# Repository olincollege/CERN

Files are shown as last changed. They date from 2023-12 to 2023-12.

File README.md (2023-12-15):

# CERN
ENGR 2110 Final Project: Centripetal Electronic Robotic Navigator (CERN)

#### Final Project by Ari Bobesh (Electrical), Venkadesh Eswaranandam (Electrical), Angela Huang (Mechancial), Sohum Kothavade (Mechanical), and Kevin Lie-Atjam (Firmware/Software)

Welcome to the Centripetal Electronic Robotic Navigator (CERN) project! In this repository, we embark on our exciting journey to build our own version of a Sphero-like robot—a small, spherical robot capable of dynamic movements and engaging interactions. Our goal was to create a Sphero-like robot with inductive charging, a custom PCB, modular and elegant design, and coherent software to control the robot.

## Dependencies and Repository Overview
This software runs on both C++ and Python. Our C++ infrastructure includes firmware for an ESP32 that can run the robot's control algorithms to drive the robot. The Python infrasture include code that is required to connect to the ESP32 over Bluetooth serial to control the robot.

## Repository Structure
The repository has a set of 4 folders which each have important information regarding the items inside of the repository

### app_interface
`app_interface` contains the Python script file required to run our control interface for our robots

### kicad
`kicad` contains a set of schematics and PCB board designs utilized in our project. Inside this folder, the `kicad.kicad_sch` file contains the transmitting circuit for the inductive charging base station. `robot.kicad_sch` and `robot.kicad_pcb` contain the circuit and PCB respectively for the receiving end of the charging circuit and the control circuitry placed inside our robot.

### motor_communicate
`motor_communicate` contains the C++ firmware required to run the robot.

### SymFoot
`SymFoot` contains footprints and symbols for our schematic with unique components not readily available in KiCAD.

### Library installation and Dependencies
To run the software, you will need the following:
* A Unix/Linux Operating System
* A Python Environment (Ex. Anaconda)
* PySerial
* Pygame
* PyBluez

To install the all of the necessary libraries, we recommend doing the following:
* Ensure that you're running a version of Python that is 3.9 or above
* Open a bash terminal on your machine
* Once it loads, I recommend creating a new Anaconda environment. This can be done by doing the following
```
conda create --name <Environment Name> python=3.9
```
Where you may name your environment whatever you would like
* Be patient and make sure that you type y to create your environment after a dialog box appears
* After the environment has been created, run the following command
```
conda activate <Environment Name>
```
To activate your Anaconda environment
* You're now ready to install the libraries to use this repository. Ensure that your file directory is at the root of this repository. By typing `ls` in the repository directory, you should see a file called `requirements.txt`. Finally, you can run the following

```
pip install -r requirements.txt
```
* Be patient and wait for the libraries to finish installing

## Robot Information
We built a set of 3 CERN Robots. The connection information and motor pinouts have been provided

| Name | MAC Address | Drive Pins | Turn Pins |
| --- | ----- | ----- | ----- |
| Stubby | 78:21:84:B9:0A:1E | A1A: 33<br /> A1B: 32<br /> B1A: 2<br /> B1B: 23<br /> Sleep: 25| A1A: 12<br /> A1B: 14<br /> B1A: 26<br /> B1B: 27<br /> Sleep: 13|
| Girthy | E0:5A:1B:E4:66:56 | A1A: 26<br /> A1B: 27<br /> B1A: 14<br /> B1B: 12<br /> Sleep: 13| A1A: 2<br /> A1B: 23<br /> B1A: 32<br /> B1B: 33<br /> Sleep: 25
| Kirby | E0:5A:1B:E4:9D:D6 | A1A: 32<br /> A1B: 33<br /> B1A: 2<br /> B1B: 23<br /> Sleep: 25| A1A: 12<br /> A1B: 14<br /> B1A: 27<br /> B1B: 26<br /> Sleep: 13

## Connecting To The Robot

These steps work best with Linux based systems

Firstly, make sure that the robot you want to connect to is on. Next, you'll want to connect to the robot by Bluetooth using the systems settings to connect to your robot. You will briefly connect to the robot, but you will then disconnect to the robot. This doesn't mean that you've lost connection, but this only means that you've placed the connection to the robot as a familiar device. Next, you're going to want to run friendly_control.py under the app_interface folder which can be executed by using the following command in a bash terminal: `python friendly_control.py` which will then ask you what device you would like to connect to. You may also open the Python script in a code editor and run the code manually. Once you run the code, it will then ask you to enter your password to because the controls will enter in root. This is because the following code is ran `sudo rfcomm bind <PORT NUMBER> <MAC ADDRESS>` which is when a radio frequency communication port will be established by your computer and robot to the Bluetooth MAC address of your robot. This is important since data is sent over serial for bluetooth. This then opens up a Pygame experience which should allow you obtain live data of the robot, control the lights of the robot, and control the robot using the WASD keys. Once you've finished driving the robot, you may close the Pygame interface, and the following command is ran: `sudo rfcomm release <PORT NUMBER>` which is when the communication port established will be dissolved, and the robot can then be reconnected or connected to another client.

If you have trouble connecting to the robot, typically running `sudo rfcomm release <PORT NUMBER>` to ensure that there doesn't exist a port that already exists that the robot tries to talk to on your computer to is typically recommended.

If you have any questions about any aspect about our project, please feel free to reach out to any of us: Ari Bobesh (abobesh@olin.edu), Kevin Lie-Atjam (klieatjam@olin.edu), Venkadesh Eswaranandam (veswaranandam@olin.edu), Sohum Kothavade (skothavade@olin.edu), and Angela Huang (ahuang3@olin.edu)

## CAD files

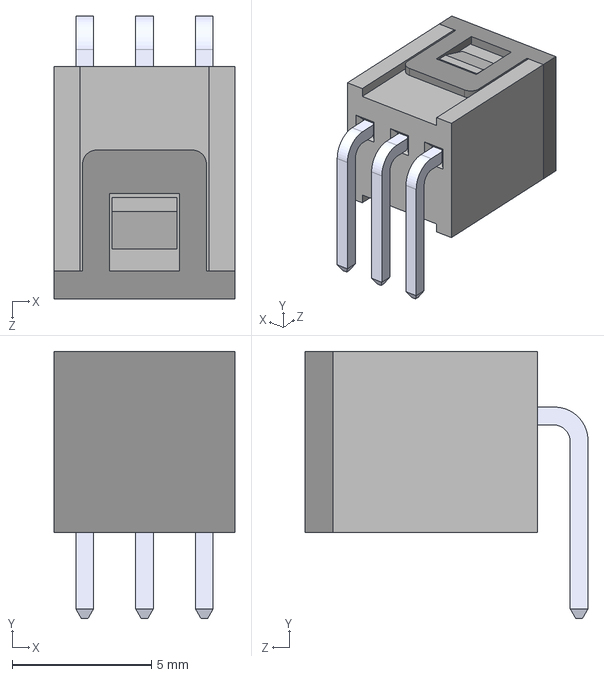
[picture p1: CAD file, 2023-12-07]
SymFoot/TM1000Q/TM1000Q.step
6.50 x 9.60 x 10.2 mm

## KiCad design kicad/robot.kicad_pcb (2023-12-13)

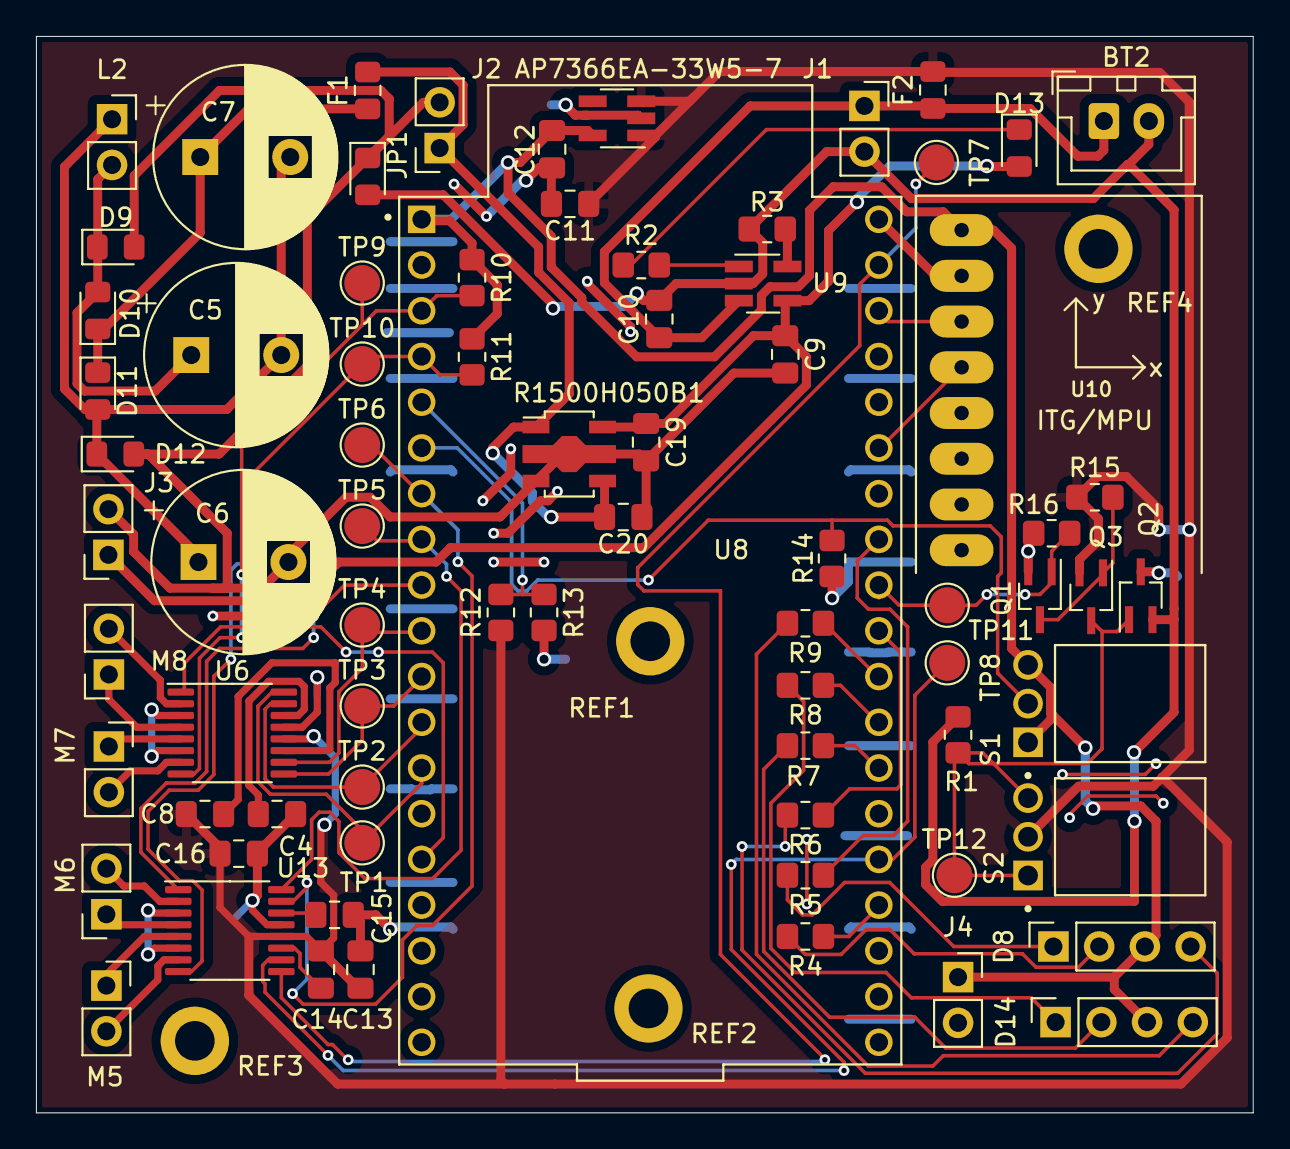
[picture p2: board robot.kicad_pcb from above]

Board: 2 copper layers, 67.6 x 59.8 mm, 79 parts (0 on the bottom side), 57 nets.

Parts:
AP7366EA-33W5-7: AP7366EA-33W5-7; SOT-23-5_HandSoldering
BT2: 1S 3000mAh; JST_XH_B2B-XH-A_1x02_P2.50mm_Vertical
C4, C15: 2.2uF,6.3V; C_0805_2012Metric_Pad1.18x1.45mm_HandSolder
C5: C; CP_Radial_D10.0mm_P5.00mm
C6, C7: 1mF; CP_Radial_D10.0mm_P5.00mm
C8, C14: 0.01uF,16V; C_0805_2012Metric_Pad1.18x1.45mm_HandSolder
C9, C10: 4.7uF; C_0805_2012Metric_Pad1.18x1.45mm_HandSolder
C11, C12: 1uF; C_0805_2012Metric_Pad1.18x1.45mm_HandSolder
C13, C16, C19: 10uF; C_0805_2012Metric_Pad1.18x1.45mm_HandSolder
C20: 0.47uF; C_0805_2012Metric_Pad1.18x1.45mm_HandSolder
D8, D14: QBL8RGB60D0-2897; PinSocket_1x04_P2.54mm_Vertical
D9, D10, D11, D12: SD0805S020S1R0; D_0805_2012Metric_Pad1.15x1.40mm_HandSolder
D13: LTST-C171GKT; LED_0805_2012Metric_Pad1.15x1.40mm_HandSolder
F1: MFU0805FF01000P100; Fuse_0805_2012Metric_Pad1.15x1.40mm_HandSolder
F2: MFU0805FF03000P100; Fuse_0805_2012Metric_Pad1.15x1.40mm_HandSolder
J1, J2, J3, J4: Adafruit Coil Jumper; PinSocket_1x02_P2.54mm_Vertical
JP1: SolderJumper_2_Open; D_0805_2012Metric_Pad1.15x1.40mm_HandSolder
L2: L; PinSocket_1x02_P2.54mm_Vertical
M5, M6, M7, M8: Motor_DC; PinSocket_1x02_P2.54mm_Vertical
Q1, Q2: DMG1012UW-7; SOT-323_SC-70_Handsoldering
Q3: DMG1013UW-7; SOT-323_SC-70_Handsoldering
R1, R10, R11, R12, R13, R14, R15, R16: 10k; R_0805_2012Metric_Pad1.20x1.40mm_HandSolder
R2: 150; R_0805_2012Metric_Pad1.20x1.40mm_HandSolder
R3: 2k; R_0805_2012Metric_Pad1.20x1.40mm_HandSolder
R4, R5, R7, R8: 5; R_0805_2012Metric_Pad1.20x1.40mm_HandSolder
R6, R9: 65; R_0805_2012Metric_Pad1.20x1.40mm_HandSolder
R1500H050B1: R1500H050B1; SOT-89-5
REF1, REF2, REF3, REF4: MountingHole_2.2mm_M2_DIN965_Pad
S1, S2: TM1000Q; SW_TM1000Q
TP1, TP2, TP3, TP4, TP5, TP6, TP7, TP8, TP9, TP10, TP11, TP12: TestPoint; TestPoint_Pad_D2.0mm
U6, U13: DRV8833PW; TSSOP-16_4.4x5mm_P0.65mm
U8: ESP32-DEVKITC; MODULE_ESP32-DEVKITC
U9: MCP73831-2-OT; SOT-23-5_HandSoldering
U10: GY-521

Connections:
/Temporary/Controller/3V3: AP7366EA-33W5-7.5 (OUT), C12.1, D8.3 (A), D14.3 (A), J4.1, R10.1, R11.1, S1.1, S1.3, U8.1 (3V3), U10.VCC
/Temporary/Controller/GND: AP7366EA-33W5-7.2 (GND), C4.1, C11.1, C12.2, C13.1, C15.1, C16.1, J4.2, Q1.2 (S), Q2.3 (D), R13.2, R14.2, R16.2, U6.3 (AISEN), U6.6 (BISEN), U6.13 (GND), U8.38 (GND3), U10.GND, U13.3 (AISEN), U13.6 (BISEN), U13.13 (GND)
/Temporary/Controller/MOSTRIG: Q1.1 (G), R16.1, TP11.1, U8.30 (IO18)
/Temporary/Controller/SCL: U8.36 (IO22), U10.SCL
/Temporary/Controller/SDA: U8.33 (IO21), U10.SDA
/Temporary/Controller/VBAT: AP7366EA-33W5-7.1 (IN), AP7366EA-33W5-7.3 (EN), C8.2, C11.2, C13.2, C14.2, C16.2, F2.2, Q3.2 (S), R12.1, R15.1, S2.2, U6.12 (VM), U13.12 (VM)
unnamed: BT2.1 (+), C10.1, F2.1, J1.1, U9.3 (V_{BAT})
unnamed: BT2.2 (-), C10.2, J1.2, JP1.2 (B), Q2.2 (S), R1.2, R3.2, U9.2 (V_{SS})
unnamed: D8.2 (BK), R4.2
unnamed: D8.1 (GK), R5.2
unnamed: D8.4 (RK), R6.2
unnamed: C5.1, D9.1 (K), D10.2 (A), L2.2
unnamed: C7.1, D10.1 (K), D11.1 (K), F1.1
unnamed: C5.2, C6.1, C7.2, D11.2 (A), D12.1 (K), L2.1
unnamed: C6.2, C9.2, C19.2, C20.2, D9.2 (A), D12.2 (A), J2.2, J3.2, JP1.1 (A), R1500H050B1.2 (GND), R1500H050B1.3 (GND)
unnamed: C9.1, C19.1, D13.2 (A), J3.1, R1500H050B1.5 (Vout), U9.4 (V_{DD})
unnamed: D13.1 (K), R2.1
unnamed: D14.2 (BK), R7.2
unnamed: D14.1 (GK), R8.2
unnamed: D14.4 (RK), R9.2
unnamed: C20.1, F1.2, J2.1, R1500H050B1.1 (Vdd), R1500H050B1.4 (CE)
unnamed: M5.1 (+), U13.5 (BOUT2)
unnamed: M5.2 (-), U13.7 (BOUT1)
unnamed: M6.1 (+), U13.4 (AOUT2)
unnamed: M6.2 (-), U13.2 (AOUT1)
unnamed: M7.1 (+), U6.5 (BOUT2)
unnamed: M7.2 (-), U6.7 (BOUT1)
unnamed: M8.1 (+), U6.4 (AOUT2)
unnamed: M8.2 (-), U6.2 (AOUT1)
unnamed: Q1.3 (D), Q3.1 (G), R15.2
unnamed: Q2.1 (G), Q3.3 (D), R1.1, S2.1, S2.3, TP12.1
unnamed: TP1.1, U6.16 (AIN1), U8.13 (IO12)
unnamed: TP2.1, U6.15 (AIN2), U8.12 (IO14)
unnamed: TP3.1, U6.9 (BIN1), U8.11 (IO27)
unnamed: TP4.1, U6.10 (BIN2), U8.10 (IO26)
unnamed: C8.1, U6.11 (VCP)
unnamed: C4.2, U6.14 (VINT)
unnamed: R10.2, TP9.1, U6.8 (nFAULT), U8.3 (SENSOR_VP)
unnamed: U6.1 (nSLEEP), U8.15 (IO13)
unnamed: R7.1, U8.26 (IO4)
unnamed: R6.1, U8.29 (IO5)
unnamed: R4.1, U8.23 (IO15)
unnamed: R8.1, U8.27 (IO16)
unnamed: R9.1, U8.28 (IO17)
unnamed: R5.1, U8.31 (IO19)
unnamed: R12.2, R13.1, U8.5 (IO34)
unnamed: R14.1, S1.2, U8.6 (IO35)
unnamed: R3.1, U9.5 (PROG)
unnamed: R2.2, U9.1 (STAT)
unnamed: TP5.1, U8.8 (IO33), U13.16 (AIN1)
unnamed: TP6.1, U8.7 (IO32), U13.15 (AIN2)
unnamed: TP7.1, U8.37 (IO23), U13.9 (BIN1)
unnamed: TP8.1, U8.24 (IO2), U13.10 (BIN2)
unnamed: C14.1, U13.11 (VCP)
unnamed: C15.2, U13.14 (VINT)
unnamed: R11.2, TP10.1, U8.4 (SENSOR_VN), U13.8 (nFAULT)
unnamed: U8.9 (IO25), U13.1 (nSLEEP)

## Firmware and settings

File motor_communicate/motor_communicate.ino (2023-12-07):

#include "BluetoothSerial.h"  // Import libaries: Bluetooth Serial and Broadcasting, IMU Readings, and PID controls
#include <Adafruit_MPU6050.h>
#include <Adafruit_Sensor.h>
#include <Wire.h>
#include <PID_v1.h>

Adafruit_MPU6050 mpu;      // Module for the IMU
BluetoothSerial SerialBT;  // Module for Bluetooth

char drive_control;
const int a1a_turn = 12;  // Pins for the turning/slow/pivotal motors
const int a1b_turn = 14; //girthy 2,23,32,33
const int b1a_turn = 27; //stubby 12,14,27,26
const int b1b_turn = 26;

const int a1a_drive = 33; // Pins for the drive/fast/forward moving motors 
const int a1b_drive = 32; //girthy 26,27,14,12
const int b1a_drive = 2; //stubby 33,32,2,23
const int b1b_drive = 23;

const int sleep_drive = 25;  // Motor sleep pins for the motor controllers
const int sleep_turn = 13;   //girthy 13,25
                             //stubby 25,13

const int R1 = 17;  // Pins for LED 1
const int G1 = 16;
const int blue1 = 4;

const int R2 = 5;  // Pins for LED 2
const int G2 = 19;
const int B2 = 15;

const int mostrig = 18;  // Pin readouts for power on and power off sequence
const int tiltread = 35;

const int power_pin = 34;
const int MPU6050_ADDR = 0x68;  // MPU6050 I2C address
const float ACC_SCALE = 16384.0; // MPU6050 accelerometer sensitivity: 16384 LSB/G
const float GYRO_SCALE = 131.0;  // MPU6050 gyroscope sensitivity: 131 LSB/°/s

unsigned long previousMillis = 0;  // Time keeping variable for power down sequence

const uint32_t IDLE_MAX = 300000;
uint32_t last_drive_input;
uint32_t t;
double batt_voltage;

//LED Stuff
bool currentlyTilted;
bool wasTilted=false;
int leftledcode[5]={0,0,0,0,0};
int rightledcode[5]={0,0,0,0,0};
int leftledcounters[2]={0,0};
int rightledcounters[2]={0,0};
int drive_power=0;
int turn_power=0;

// Variables to store the state and timing information
bool tilted = true;
bool shutdown = false;
unsigned long tiltStartTime = 0;
unsigned long tiltDuration = 5000;  // 5 seconds in milliseconds
int counter = 0;

void forward(int power_drive);  // These six functions are resposible for controlling the robot in whatever direction the user commands it to
void backwards(int power_drive);
void stop_drive();
void right(int power_turn);
void left(int power_turn);
void stop_turn();

void kill_power();  // Turn off the robot

void light_test(int power_turn);

void setup() {
  Serial.begin(115200);
  SerialBT.begin("Stubby");  // When turned on, start broadcasting a Bluetooth module that everyone can see and connect to

  delay(500);
  batt_voltage=(double)analogRead(power_pin)*2/1158;
  pinMode(mostrig, OUTPUT);
  if(batt_voltage>3.3)
  {
    digitalWrite(mostrig, 1);  // Activate the mostrig pin which tells the robot to power on
  }
  else
  {
    for(int i=0; i<10; i++)
    {
      analogWrite(R2, 255);
      analogWrite(R1, 0);
      delay(20);
      analogWrite(R1, 255);
      analogWrite(R2, 0);
      delay(20);
    }
  }
  pinMode(tiltread, INPUT);

  pinMode(a1a_drive, OUTPUT);  // Set all motor output pins as a PWM output to drive the motor
  pinMode(a1b_drive, OUTPUT);
  pinMode(b1a_drive, OUTPUT);
  pinMode(b1b_drive, OUTPUT);

  pinMode(a1a_turn, OUTPUT);
  pinMode(a1b_turn, OUTPUT);
  pinMode(b1a_turn, OUTPUT);
  pinMode(b1b_turn, OUTPUT);

  analogWrite(a1a_drive, 0);
  analogWrite(a1b_drive, 0);
  analogWrite(b1a_drive, 0);
  analogWrite(b1b_drive, 0);

  analogWrite(a1a_turn, 0);
  analogWrite(a1b_turn, 0);
  analogWrite(b1a_turn, 0);
  analogWrite(b1b_turn, 0);

  pinMode(sleep_drive, OUTPUT);  // Set the motor sleep controller as digital outputs and initialize to low to be off
  pinMode(sleep_turn, OUTPUT);

  digitalWrite(sleep_drive, 0);
  digitalWrite(sleep_turn, 0);

  pinMode(R1,OUTPUT); /* Go through a lighting sequence to notify the user that the IMU is reading. 
                         A green light will activate telling the user that the setup is complete*/
  pinMode(G1,OUTPUT);
  pinMode(blue1,OUTPUT);
  pinMode(R2,OUTPUT);
  pinMode(G2,OUTPUT);
  pinMode(B2,OUTPUT);
  
  analogWrite(G1, 0);
  analogWrite(blue1, 255);
  Wire.begin(); // Initialize comunication
  Wire.beginTransmission(MPU6050_ADDR);
  Wire.write(0x6B);  // PWR_MGMT_1 register
  Wire.write(0);     // Clear the sleep bit
  Wire.endTransmission(true);

  last_drive_input=millis();

  analogWrite(R2, 255);
  analogWrite(G2, 255);

  // Once the green light has been turned on, the setup is complete
}


void loop() {
  /* The loop is active when the user is connected to the robot via the control application that sends
  commands over Bluetooth serial to control the robot through WASD keys */

  String steering_controls = SerialBT.readStringUntil('\n');
  /* Over the serial, every user control has two comma separated integers ranging from -255 to 255 for both integers.
  The leftmost integer represents the respective motor control for the forward driving motors while the rightmost
  integer is the turning motor power. */

  parse_input(steering_controls);
  float y_accel = 0.0;

  for (int record = 0; record < 50; record++){
    float accelX_G, accelY_G, accelZ_G, gyroX_rad, gyroY_rad, gyroZ_rad;
    readMPU6050Data(accelX_G, accelY_G, accelZ_G, gyroX_rad, gyroY_rad, gyroZ_rad);
    y_accel = y_accel + accelY_G;
  }

  y_accel = y_accel/50;
  if ((drive_power!=0) && (abs(y_accel) > 0.15)){
    if (y_accel > 0){
      turn_power = turn_power - 60 - 120*y_accel;
      if (turn_power < -255){
        turn_power = -255;
      }
    } else if (y_accel < 0){
      turn_power = turn_power + 60 + 120*y_accel;
      if (turn_power > 255){
        turn_power = 255;
      }
    }

  }


  if (drive_power > 0) {
    forward(drive_power);  // If the user is pressing W on their keyboard, the user would like to move forward and so the first integer is positive.
  } else if (drive_power < 0) {
    backwards(drive_power * -1);  // If the user instead presses S, the user would like to move backwards which means that the motor power is negative.
  } else {
    stop_drive();  // If the user presses neither, the integer will be zero and the motor driver for the forward motors should be put to sleep.
  }

  if (turn_power > 0) {
    right(turn_power);  // If the user is pressing D on their keyboard, the user would like to turn right so the second integer is positive.
  } else if (turn_power < 0) {
    left(turn_power * -1);  // If the user is pressing A on their keyboard, the user would like to turn left so the second integer is negative.
  } else {
    stop_turn();  // Like the drive motors, if neither is pressed, the second integer will be zero, and motor controls should not be sent to the turn motors.
  }
  led_control();
  batt_voltage=(double)analogRead(power_pin)*2/1158;
  SerialBT.println(batt_voltage);
  kill_power();  // At the end of the loop, run this function to see if the user would like to shut off the robot
}

/*
** Returns a boolean value that indicates whether the current time, t, is later than some prior
** time, t0, plus a given interval, dt.  The condition accounts for timer overflow / wraparound.
*/
bool it_is_time(uint32_t t, uint32_t t0, uint32_t dt) {
  return ((t >= t0) && (t - t0 >= dt)) ||         // The first disjunct handles the normal case
         ((t < t0) && (t + (~t0) + 1 >= dt));  //   while the second handles the overflow case
}

void readMPU6050Data(float &accelX_G, float &accelY_G, float &accelZ_G, float &gyroX_rad, float &gyroY_rad, float &gyroZ_rad) {
  Wire.beginTransmission(MPU6050_ADDR);
  Wire.write(0x3B);  // Starting register for accelerometer data
  Wire.endTransmission(false);
  Wire.requestFrom(MPU6050_ADDR, 14, true);  // Request 14 bytes of data
  int16_t accelX, accelY, accelZ, gyroX, gyroY, gyroZ;

  accelX = Wire.read() << 8 | Wire.read();
  accelY = Wire.read() << 8 | Wire.read();
  accelZ = Wire.read() << 8 | Wire.read();

  Wire.read();  // Skip 2 bytes of temperature data

  gyroX = Wire.read() << 8 | Wire.read();
  gyroY = Wire.read() << 8 | Wire.read();
  gyroZ = Wire.read() << 8 | Wire.read();

  accelX_G = accelX / ACC_SCALE;
  accelY_G = accelY / ACC_SCALE;
  accelZ_G = accelZ / ACC_SCALE;

  // Normalize gyroscope data to radians per second
  gyroX_rad = gyroX / GYRO_SCALE * 57.2958;
  gyroY_rad = gyroY / GYRO_SCALE * 57.2958;
  gyroZ_rad = gyroZ / GYRO_SCALE * 57.2958;
}

void parse_input(String input)
{
  int currentindex=-1;
  int numbercount=1;
  while(true)
  {
    int nextindex=input.indexOf(',',currentindex+1);
    if(nextindex==-1)
    {
      if(numbercount==1)
      {
        break;
      }
      String sub = input.substring(currentindex+1, input.length()); 
      if(sub.equals("shutdown"))
      {
        initiate_shutdown();
        break;
      }
      assign_input(sub.toInt(),numbercount);
      break;
    }
    String sub = input.substring(currentindex+1, nextindex); 
    assign_input(sub.toInt(),numbercount);
    numbercount++;
    currentindex=nextindex;
  }
}

void assign_input(int value, int numbercount)
{
  switch(numbercount)
  {
    case 1: //drive power
      drive_power=value;
      break;
    case 2: //turn power
      turn_power=value;
      break;
    default:
      if(numbercount<8)
      {
        leftledcode[(numbercount-3)%5]=value;
      }
      else
      {
        rightledcode[(numbercount-3)%5]=value;
      }
      break;
  }
}

void led_control()
{
//  int leftledcode[5];
//int rightledcode[5];
//int leftledcounters[2];
//int rightledcounters[2];
//const int R1 = 17; // Pins for LED 1
//const int G1 = 16;
//const int blue1 = 4;
//
//const int R2 = 5; // Pins for LED 2
//const int G2 = 19;
//const int B2 = 15;
  if(!currentlyTilted)
  {
    wasTilted=false;
    //Left LED
    if(leftledcounters[0]<leftledcode[3])
    {
      analogWrite(R1,255-leftledcode[0]);
      analogWrite(G1,255-leftledcode[1]);
      analogWrite(blue1,255-leftledcode[2]);
      leftledcounters[0]++;
    }
    else if (leftledcounters[1]<leftledcode[4])
    {
      analogWrite(R1,255);
      analogWrite(G1,255);
      analogWrite(blue1,255);
      leftledcounters[1]++;
    }
    else
    {
      leftledcounters[0]=0;
      leftledcounters[1]=0;
    }
    //Right LED
    if(rightledcounters[0]<rightledcode[3])
    {
      analogWrite(R2,255-rightledcode[0]);
      analogWrite(G2,255-rightledcode[1]);
      analogWrite(B2,255-rightledcode[2]);
      rightledcounters[0]++;
    }
    else if (rightledcounters[1]<rightledcode[4])
    {
      analogWrite(R2,255);
      analogWrite(G2,255);
      analogWrite(B2,255);
      rightledcounters[1]++;
    }
    else
    {
      rightledcounters[0]=0;
      rightledcounters[1]=0;
    }
  }
  else
  {
    if(!wasTilted)
    {
      analogWrite(R1,255);
      analogWrite(G1,255);
      analogWrite(blue1,255);
      analogWrite(R2,255);
      analogWrite(G2,255);
      analogWrite(B2,255);
    }
    wasTilted=true;
  }
}

void forward(int power_drive) {  // Run the robot forward by turning on the motor controller and setting the two positive inputs at a higher voltage.
  digitalWrite(sleep_drive, 1);
  analogWrite(a1a_drive, power_drive);
  analogWrite(b1a_drive, power_drive);
  analogWrite(a1b_drive, 0);
  analogWrite(b1b_drive, 0);
  last_drive_input=millis();
}

void backwards(int power_drive) {  // Run the robot backwards by turning on the motor controller and setting the two negative inputs at a higher voltage.
  digitalWrite(sleep_drive, 1);
  analogWrite(a1a_drive, 0);
  analogWrite(b1a_drive, 0);
  analogWrite(a1b_drive, power_drive);
  analogWrite(b1b_drive, power_drive);
  last_drive_input=millis();
}

void stop_drive() {  // Stop the robot by turning off the motor controller and setting each of the drive pins to 0 volts.
  digitalWrite(sleep_drive, 0);
  analogWrite(a1a_drive, 0);
  analogWrite(b1a_drive, 0);
  analogWrite(a1b_drive, 0);
  analogWrite(b1b_drive, 0);
}

void right(int power_turn) {  // Turn the robot right by turning on the motor controller and setting the two positive inputs at a higher voltage.
  digitalWrite(sleep_turn, 1);
  analogWrite(b1a_turn, 0);
  analogWrite(a1b_turn, 0);
  analogWrite(a1a_turn, power_turn);
  analogWrite(b1b_turn, power_turn);
}

void left(int power_turn) {  // Turn the robot left by turning on the motor controller and setting the two negative inputs at a higher voltage.
  digitalWrite(sleep_turn, 1);
  analogWrite(b1a_turn, power_turn);
  analogWrite(a1b_turn, power_turn);
  analogWrite(a1a_turn, 0);
  analogWrite(b1b_turn, 0);
}

void stop_turn() {  // Stop the turning of the robot by turning off the motor controllers and setting each of the turn pins to 0 volts.
  digitalWrite(sleep_turn, 0);
  analogWrite(b1a_turn, 0);
  analogWrite(a1b_turn, 0);
  analogWrite(a1a_turn, 0);
  analogWrite(b1b_turn, 0);
}

void kill_power(){ // Run through the sequence of  checking to see if the user would turn off the robot

  currentlyTilted = (digitalRead(tiltread) == HIGH);

  if (currentlyTilted) // Read the state of the tilt switch. If it is tilted approximately 60 degrees, the second green light will switch on
  {
//    digitalWrite(R2,0);
    analogWrite(G2,0);
  }
  else
  {
//    digitalWrite(R2,1);
//    digitalWrite(G2,0); // If not, the tilt switch will cause the green second light to turn on.
  }
  if (currentlyTilted != tilted) { // If the robot switches from being in a non tilted state to a tilted state, then start a timer
    // Tilt state has changed
    tilted = currentlyTilted;
    tiltStartTime = millis();  // Update the tilt start time
  }

  if (tilted && ((millis() - tiltStartTime) >= tiltDuration)) { 
    /* If the amount of time the robot has been tilted for is greater than or equal to 5 seconds, 
    then run the shutoff command. */
    initiate_shutdown();

  } 
  else if(!tilted && shutdown && ((millis() - tiltStartTime) >= tiltDuration/5)) // Once the robot has been tilted for more than 5 seconds, the robot has to be tilted up again to kill the power
  {
    digitalWrite(mostrig, LOW);
  }
  if (it_is_time(millis(), last_drive_input, IDLE_MAX))
  {
    initiate_shutdown();
  }

  // Small delay to avoid excessive loop iteration
  delay(10);
} 

void initiate_shutdown()
{
    shutdown = true; // Tilted for more than 5 seconds, assert LOW on tilt switch pin
//    digitalWrite(G1,1);
    analogWrite(blue1, 0); // Flash the blue light to notify the user that the robot is about to turn off
    delay(500);
    analogWrite(blue1, 255);
}

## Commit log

2023-10-21 Add induction charging circuit
    [induction.kicad_sch, kicad.kicad_pcb, kicad.kicad_sch]
2023-10-21 Fix transistors on charge management
    [induction.kicad_sch]
2023-10-22 Add pulldown resistors
    [induction.kicad_sch]
2023-10-22 Create subcircuit sheets
    [Ilimiter.kicad_sch, battvoltagedetect.kicad_sch, crowbar.kicad_sch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]
2023-10-22 Subdivide circuits into hierarchical sheets
    [Ilimiter.kicad_sch, crowbar.kicad_sch, xtal.kicad_sch]
2023-10-23 Add inverter driver
    [PPRI.kicad_sch, induction.kicad_sch, xtal.kicad_sch]
2023-10-23 Add robot schematic
    [robot.kicad_sch]
2023-10-23 Add SymFoots
    [birdsarentreal.kicad_sch, robot.kicad_sch]
2023-10-24 Finish Robot Schematic
    [birdsarentreal.kicad_sch, controller.kicad_sch]
2023-10-24 Add capacitors
    [birdsarentreal.kicad_sch]
2023-10-25 Add all symbols and values
    [birdsarentreal.kicad_sch, controller.kicad_sch, robot.kicad_sch]
2023-10-25 Fix footprints
    [birdsarentreal.kicad_sch, controller.kicad_sch, robot.kicad_pcb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]
2023-10-26 Add board layout
    [birdsarentreal.kicad_sch, controller.kicad_sch, robot.kicad_pcb]
2023-10-26 Start adding PCB traces
    [robot.kicad_pcb]
2023-10-26 So many DRC errors
    [birdsarentreal.kicad_sch, controller.kicad_sch, robot.kicad_pcb]
2023-10-26 Add new 3.3V regulator
    [birdsarentreal.kicad_sch, robot.kicad_pcb]
2023-10-27 Add tilt switch
    [TM1000Q.step, birdsarentreal.kicad_sch, controller.kicad_sch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]
2023-10-27 First PCB Layout complete
    [birdsarentreal.kicad_sch, robot.kicad_pcb]
2023-10-27 Add mounting holes
    [robot.kicad_pcb]
2023-10-29 Fix banned pins on ESP32
    [birdsarentreal.kicad_sch, controller.kicad_sch]
2023-10-29 Republish PCB footprint
    [robot.kicad_pcb]
2023-10-29 Make schematic pretty
    [birdsarentreal.kicad_sch, controller.kicad_sch, robot.kicad_pcb]
2023-10-29 Cleaned up ground traces
    [robot.kicad_pcb]
2023-10-31 Fix MOSFET footprint pinout
    [birdsarentreal.kicad_sch, robot.kicad_pcb]
2023-11-01 Change battery connector
    [birdsarentreal.kicad_sch, robot.kicad_pcb]
2023-11-04 Final PCB
    [birdsarentreal.kicad_sch, controller.kicad_sch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]
2023-12-03 Add LED control
2023-12-04 Fix small integration issues for LEDs
    [motor_communicate.ino]
2023-12-05 Code instantiated for x-axis correction
    [motor_communicate.ino]
2023-12-15 Update induction charging schematic
    [Ilimiter.kicad_sch, PPRI.kicad_sch, battvoltagedetect.kicad_sch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]
